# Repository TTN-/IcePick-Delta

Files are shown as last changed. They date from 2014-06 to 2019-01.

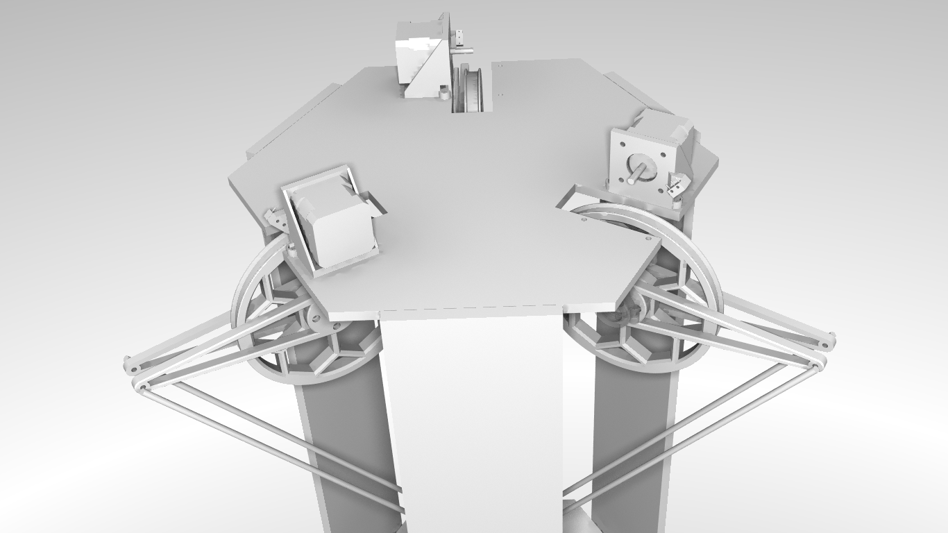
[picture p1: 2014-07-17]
Icepick Delta/Beta/Jotham/renders/assembly4.png

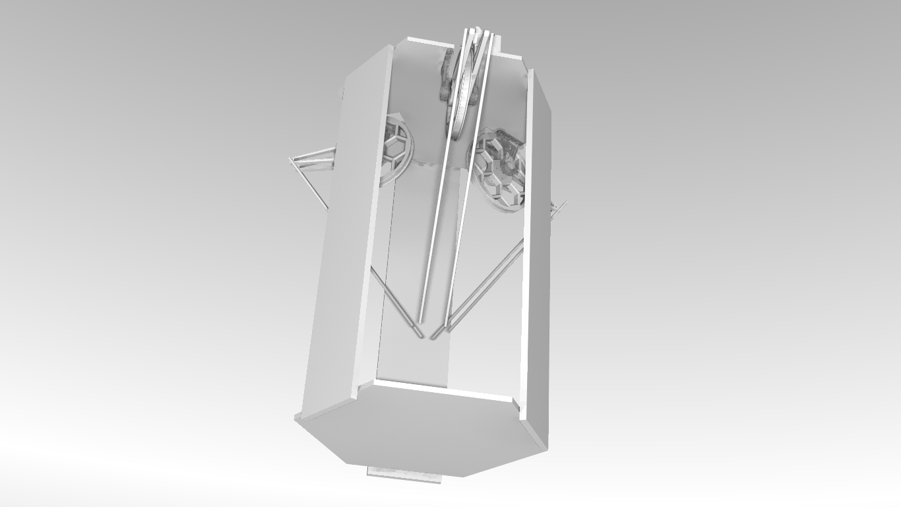
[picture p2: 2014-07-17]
Icepick Delta/Beta/Jotham/renders/assembly3.png

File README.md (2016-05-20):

IcePick Delta CAD files
=======================
I should state that this printer is NOT ready for general consumption and is HIGHLY experimental. 

Most of these parts are still being tested and revised, they may be improved without prior notice ;)

More details at the <a href="http://hackaday.io/project/1565">Icepick-delta HackaDay page.</a>

Firmware
========
Firmware for the Icepick-Delta can be found <a href="https://github.com/Laura3/Marlin/tree/Marlin_v1"> here.</a>

Contributors/Credits
============
Lots of thanks goes to the Firepick Delta team, (<a href=http://hackaday.io/project/963> project page</a> ) for being the original inspiration to this project. Thank you Lerche, Neil Jansen, Karl, Lew and Dayton Pidhirney. Without you guys this project wouldn't have existed.

Credit goes to Matt Kimbal for pulley_mounts.stl
Pulley_mount.stl and pulley_mount.FCStd are copyright of Matt Kimbal, released under gpl version 3.

Credit goes to Johann Rochell for effector.stl and effector_retractable.stl from his <a href="https://github.com/jcrocholl/kossel">Github Kossel repository.</a> are copyright of Johann Rochell, released under gpl version 3.

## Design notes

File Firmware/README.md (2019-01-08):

Marlin Firmware for Non-linear Delta 3D Printers
==================================================
This firmware is a fork of the main repository with modifications for non-linear delta printers such as the
<a href="http://hackaday.io/project/1565">Icepick Delta</a>. 

==========================
Marlin 3D Printer Firmware
==========================
Marlin has a GPL license because I believe in open development.
Please do not use this code in products (3D printers, CNC etc) that are closed source or are crippled by a patent.



Quick Information
===================
This RepRap firmware is a mashup between <a href="https://github.com/kliment/Sprinter">Sprinter</a>, <a href="https://github.com/simen/grbl/tree">grbl</a> and many original parts.

Derived from Sprinter and Grbl by Erik van der Zalm.
Sprinters lead developers are Kliment and caru.
Grbls lead developer is Simen Svale Skogsrud. Sonney Jeon (Chamnit) improved some parts of grbl
A fork by bkubicek for the Ultimaker was merged, and further development was aided by him.
Some features have been added by:
Lampmaker, Bradley Feldman, and others...

Features:

*   Interrupt based movement with real linear acceleration
*   High steprate
*   Look ahead (Keep the speed high when possible. High cornering speed)
*   Interrupt based temperature protection
*   preliminary support for Matthew Roberts advance algorithm
    For more info see: http://reprap.org/pipermail/reprap-dev/2011-May/003323.html
*   Full endstop support
*   SD Card support
*   SD Card folders (works in pronterface)
*   SD Card autostart support
*   LCD support (ideally 20x4)
*   LCD menu system for autonomous SD card printing, controlled by an click-encoder.
*   EEPROM storage of e.g. max-velocity, max-acceleration, and similar variables
*   many small but handy things originating from bkubicek's fork.
*   Arc support
*   Temperature oversampling
*   Dynamic Temperature setpointing aka "AutoTemp"
*   Support for QTMarlin, a very beta GUI for PID-tuning and velocity-acceleration testing. https://github.com/bkubicek/QTMarlin
*   Endstop trigger reporting to the host software.
*   Updated sdcardlib
*   Heater power reporting. Useful for PID monitoring.
*   PID tuning
*   CoreXY kinematics (www.corexy.com/theory.html)
*   Delta kinematics
*   Dual X-carriage support for multiple extruder systems
*   Configurable serial port to support connection of wireless adaptors.
*   Automatic operation of extruder/cold-end cooling fans based on nozzle temperature
*   RC Servo Support, specify angle or duration for continuous rotation servos.
*   Bed Auto Leveling.

The default baudrate is 250000. This baudrate has less jitter and hence errors than the usual 115200 baud, but is less supported by drivers and host-environments.

Differences and additions to the already good Sprinter firmware:
================================================================

*Look-ahead:*

Marlin has look-ahead. While sprinter has to break and re-accelerate at each corner,
lookahead will only decelerate and accelerate to a velocity,
so that the change in vectorial velocity magnitude is less than the xy_jerk_velocity.
This is only possible, if some future moves are already processed, hence the name.
It leads to less over-deposition at corners, especially at flat angles.

*Arc support:*

Slic3r can find curves that, although broken into segments, were ment to describe an arc.
Marlin is able to print those arcs. The advantage is the firmware can choose the resolution,
and can perform the arc with nearly constant velocity, resulting in a nice finish.
Also, less serial communication is needed.

*Temperature Oversampling:*

To reduce noise and make the PID-differential term more useful, 16 ADC conversion results are averaged.

*AutoTemp:*

If your gcode contains a wide spread of extruder velocities, or you realtime change the building speed, the temperature should be changed accordingly.
Usually, higher speed requires higher temperature.
This can now be performed by the AutoTemp function
By calling M109 S<mintemp> T<maxtemp> F<factor> you enter the autotemp mode.

You can leave it by calling M109 without any F.
If active, the maximal extruder stepper rate of all buffered moves will be calculated, and named "maxerate" [steps/sec].
The wanted temperature then will be set to t=tempmin+factor*maxerate, while being limited between tempmin and tempmax.
If the target temperature is set manually or by gcode to a value less then tempmin, it will be kept without change.
Ideally, your gcode can be completely free of temperature controls, apart from a M109 S T F in the start.gcode, and a M109 S0 in the end.gcode.

*EEPROM:*

If you know your PID values, the acceleration and max-velocities of your unique machine, you can set them, and finally store them in the EEPROM.
After each reboot, it will magically load them from EEPROM, independent what your Configuration.h says.

*LCD Menu:*

If your hardware supports it, you can build yourself a LCD-CardReader+Click+encoder combination. It will enable you to realtime tune temperatures,
accelerations, velocities, flow rates, select and print files from the SD card, preheat, disable the steppers, and do other fancy stuff.
One working hardware is documented here: http://www.thingiverse.com/thing:12663
Also, with just a 20x4 or 16x2 display, useful data is shown.

*SD card folders:*

If you have an SD card reader attached to your controller, also folders work now. Listing the files in pronterface will show "/path/subpath/file.g".
You can write to file in a subfolder by specifying a similar text using small letters in the path.
Also, backup copies of various operating systems are hidden, as well as files not ending with ".g".

*SD card folders:*

If you place a file auto[0-9].g into the root of the sd card, it will be automatically executed if you boot the printer. The same file will be executed by selecting "Autostart" from the menu.
First *0 will be performed, than *1 and so on. That way, you can heat up or even print automatically without user interaction.

*Endstop trigger reporting:*

If an endstop is hit while moving towards the endstop, the location at which the firmware thinks that the endstop was triggered is outputed on the serial port.
This is useful, because the user gets a warning message.
However, also tools like QTMarlin can use this for finding acceptable combinations of velocity+acceleration.

*Coding paradigm:*

Not relevant from a user side, but Marlin was split into thematic junks, and has tried to partially enforced private variables.
This is intended to make it clearer, what interacts which what, and leads to a higher level of modularization.
We think that this is a useful prestep for porting this firmware to e.g. an ARM platform in the future.
A lot of RAM (with enabled LCD ~2200 bytes) was saved by storing char []="some message" in Program memory.
In the serial communication, a #define based level of abstraction was enforced, so that it is clear that
some transfer is information (usually beginning with "echo:"), an error "error:", or just normal protocol,
necessary for backwards compatibility.

*Interrupt based temperature measurements:*

An interrupt is used to manage ADC conversions, and enforce checking for critical temperatures.
This leads to less blocking in the heater management routine.

Implemented G Codes:
====================

*  G0  -> G1
*  G1  - Coordinated Movement X Y Z E
*  G2  - CW ARC
*  G3  - CCW ARC
*  G4  - Dwell S<seconds> or P<milliseconds>
*  G10 - retract filament according to settings of M207
*  G11 - retract recover filament according to settings of M208
*  G28 - Home all Axis
*  G29 - Detailed Z-Probe, probes the bed at 3 points.  You must de at the home position for this to work correctly.
*  G30 - Single Z Probe, probes bed at current XY location.
*  G90 - Use Absolute Coordinates
*  G91 - Use Relative Coordinates
*  G92 - Set current position to cordinates given

M Codes
*  M0   - Unconditional stop - Wait for user to press a button on the LCD (Only if ULTRA_LCD is enabled)
*  M1   - Same as M0
*  M17  - Enable/Power all stepper motors
*  M18  - Disable all stepper motors; same as M84
*  M20  - List SD card
*  M21  - Init SD card
*  M22  - Release SD card
*  M23  - Select SD file (M23 filename.g)
*  M24  - Start/resume SD print
*  M25  - Pause SD print
*  M26  - Set SD position in bytes (M26 S12345)
*  M27  - Report SD print status
*  M28  - Start SD write (M28 filename.g)
*  M29  - Stop SD write
*  M30  - Delete file from SD (M30 filename.g)
*  M31  - Output time since last M109 or SD card start to serial
*  M32  - Select file and start SD print (Can be used when printing from SD card)
*  M42  - Change pin status via gcode Use M42 Px Sy to set pin x to value y, when omitting Px the onboard led will be used.
*  M80  - Turn on Power Supply
*  M81  - Turn off Power Supply
*  M82  - Set E codes absolute (default)
*  M83  - Set E codes relative while in Absolute Coordinates (G90) mode
*  M84  - Disable steppers until next move, or use S<seconds> to specify an inactivity timeout, after which the steppers will be disabled.  S0 to disable the timeout.
*  M85  - Set inactivity shutdown timer with parameter S<seconds>. To disable set zero (default)
*  M92  - Set axis_steps_per_unit - same syntax as G92
*  M104 - Set extruder target temp
*  M105 - Read current temp
*  M106 - Fan on
*  M107 - Fan off
*  M109 - Sxxx Wait for extruder current temp to reach target temp. Waits only when heating
*         Rxxx Wait for extruder current temp to reach target temp. Waits when heating and cooling
*  M114 - Output current position to serial port
*  M115 - Capabilities string
*  M117 - display message
*  M119 - Output Endstop status to serial port
*  M126 - Solenoid Air Valve Open (BariCUDA support by jmil)
*  M127 - Solenoid Air Valve Closed (BariCUDA vent to atmospheric pressure by jmil)
*  M128 - EtoP Open (BariCUDA EtoP = electricity to air pressure transducer by jmil)
*  M129 - EtoP Closed (BariCUDA EtoP = electricity to air pressure transducer by jmil)
*  M140 - Set bed target temp
*  M190 - Sxxx Wait for bed current temp to reach target temp. Waits only when heating
*         Rxxx Wait for bed current temp to reach target temp. Waits when heating and cooling
*  M200 - Set filament diameter
*  M201 - Set max acceleration in units/s^2 for print moves (M201 X1000 Y1000)
*  M202 - Set max acceleration in units/s^2 for travel moves (M202 X1000 Y1000) Unused in Marlin!!
*  M203 - Set maximum feedrate that your machine can sustain (M203 X200 Y200 Z300 E10000) in mm/sec
*  M204 - Set default acceleration: S normal moves T filament only moves (M204 S3000 T7000) im mm/sec^2  also sets minimum segment time in ms (B20000) to prevent buffer underruns and M20 minimum feedrate
*  M205 -  advanced settings:  minimum travel speed S=while printing T=travel only,  B=minimum segment time X= maximum xy jerk, Z=maximum Z jerk, E=maximum E jerk
*  M206 - set additional homeing offset
*  M207 - set retract length S[positive mm] F[feedrate mm/sec] Z[additional zlift/hop]
*  M208 - set recover=unretract length S[positive mm surplus to the M207 S*] F[feedrate mm/sec]
*  M209 - S<1=true/0=false> enable automatic retract detect if the slicer did not support G10/11: every normal extrude-only move will be classified as retract depending on the direction.
*  M218 - set hotend offset (in mm): T<extruder_number> X<offset_on_X> Y<offset_on_Y>
*  M220 S<factor in percent>- set speed factor override percentage
*  M221 S<factor in percent>- set extrude factor override percentage
*  M240 - Trigger a camera to take a photograph
*  M280 - Position an RC Servo P<index> S<angle/microseconds>, ommit S to report back current angle
*  M300 - Play beepsound S<frequency Hz> P<duration ms>
*  M301 - Set PID parameters P I and D
*  M302 - Allow cold extrudes
*  M303 - PID relay autotune S<temperature> sets the target temperature. (default target temperature = 150C)
*  M304 - Set bed PID parameters P I and D
*  M400 - Finish all moves
*  M401 - Lower z-probe if present
*  M402 - Raise z-probe if present
*  M500 - stores paramters in EEPROM
*  M501 - reads parameters from EEPROM (if you need reset them after you changed them temporarily).
*  M502 - reverts to the default "factory settings".  You still need to store them in EEPROM afterwards if you want to.
*  M503 - print the current settings (from memory not from eeprom)
*  M540 - Use S[0|1] to enable or disable the stop SD card print on endstop hit (requires ABORT_ON_ENDSTOP_HIT_FEATURE_ENABLED)
*  M600 - Pause for filament change X[pos] Y[pos] Z[relative lift] E[initial retract] L[later retract distance for removal]
*  M907 - Set digital trimpot motor current using axis codes.
*  M908 - Control digital trimpot directly.
*  M350 - Set microstepping mode.
*  M351 - Toggle MS1 MS2 pins directly.
*  M928 - Start SD logging (M928 filename.g) - ended by M29
*  M999 - Restart after being stopped by error

Configuring and compilation:
============================

Install the arduino software IDE/toolset v23 (Some configurations also work with 1.x.x)
   http://www.arduino.cc/en/Main/Software

Download the Marlin firmware
   https://github.com/ErikZalm/Marlin/tree/Marlin_v1
   Use the "Download Zip" button on the right.

For gen6/gen7 and sanguinololu the Sanguino directory in the Marlin dir needs to be copied to the arduino environment.
  copy ArduinoAddons\Arduino_x.x.x\sanguino <arduino home>\hardware\Sanguino

Start the arduino IDE.
Select Tools -> Board -> Arduino Mega 2560    or your microcontroller
Select the correct serial port in Tools ->Serial Port
Open Marlin.pde

Click the Verify/Compile button

Click the Upload button
If all goes well the firmware is uploading

That's ok.  Enjoy Silky Smooth Printing.

===============================================
Instructions for configuring Bed Auto Leveling
===============================================
Uncomment the "ENABLE_AUTO_BED_LEVELING" define (commented by default)

You will probably need a swivel Z-MIN endstop in the extruder. A rc servo do a great job.
Check the system working here: http://www.youtube.com/watch?v=3IKMeOYz-1Q (Enable English subtitles)
Teasing ;-) video: http://www.youtube.com/watch?v=x8eqSQNAyro

In order to get the servo working, you need to enable:

* \#define NUM_SERVOS 1 // Servo index starts with 0 for M280 command

* \#define SERVO_ENDSTOPS {-1, -1, 0} // Servo index for X, Y, Z. Disable with -1

* \#define SERVO_ENDSTOP_ANGLES {0,0, 0,0, 165,60} // X,Y,Z Axis Extend and Retract angles

The first define tells firmware how many servos you have.
The second tells what axis this servo will be attached to. In the example above, we have a servo in Z axis.
The third one tells the angle in 2 situations: Probing (165º) and resting (60º). Check this with command M280 P0 S{angle} (example: M280 P0 S60 moves the servo to 60º)

*For RAMPS users:*
By default, RAMPS have no power on servo bus (if you happen to have a multimeter, check the voltage on servo power pins).
In order to get the servo working, you need to supply 5V to 5V pin.. You can do it using your power supply (if it has a 5V output) or jumping the "Vcc" from Arduino to the 5V RAMPS rail.
These 2 pins are located just between the Reset Button and the yellow fuses... There are marks in the board showing 5V and VCC.. just connect them..
If jumping the arduino Vcc do RAMPS 5V rail, take care to not use a power hungry servo, otherwise you will cause a blackout in the arduino board ;-)

Next you need to define the Z endstop (probe) offset from hotend.
My preferred method:

* a) Make a small mark in the bed with a marker/felt-tip pen.
* b) Place the hotend tip as *exactly* as possible on the mark, touching the bed. Raise the hotend 0.1mm (a regular paper thickness) and zero all axis (G92 X0 Y0 Z0);
* d) Raise the hotend 10mm (or more) for probe clearance, lower the Z probe (Z-Endstop) with M401 and place it just on that mark by moving X, Y and Z;
* e) Lower the Z in 0.1mm steps, with the probe always touching the mark (it may be necessary to adjust X and Y as well) until you hear the "click" meaning the mechanical endstop was trigged. You can confirm with M119;
* f) Now you have the probe in the same place as your hotend tip was before. Perform a M114 and write down the values, for example: X:24.3 Y:-31.4 Z:5.1;
* g) You can raise the z probe with M402 command;
* h) Fill the defines bellow multiplying the values by "-1" (just change the signal)

* \#define X_PROBE_OFFSET_FROM_EXTRUDER -24.3
* \#define Y_PROBE_OFFSET_FROM_EXTRUDER 31.4
* \#define Z_PROBE_OFFSET_FROM_EXTRUDER -5.1

The following options define the probing positions. These are good starting values.
I recommend to keep a better clearance from borders in the first run and then make the probes as close as possible to borders:

* \#define LEFT_PROBE_BED_POSITION 30
* \#define RIGHT_PROBE_BED_POSITION 140
* \#define BACK_PROBE_BED_POSITION 140
* \#define FRONT_PROBE_BED_POSITION 30

A few more options:

* \#define XY_TRAVEL_SPEED 6000

X and Y axis travel speed between probes, in mm/min.
Bear in mind that really fast moves may render step skipping. 6000 mm/min (100mm/s) is a good value.

* \#define Z_RAISE_BEFORE_PROBING 10
* \#define Z_RAISE_BETWEEN_PROBINGS 10

The Z axis is lifted when traveling to the first probe point by Z_RAISE_BEFORE_PROBING value
and then lifted when traveling from first to second and second to third point by Z_RAISE_BETWEEN_PROBINGS.
All values are in mm as usual. 

That's it.. enjoy never having to calibrate your Z endstop neither leveling your bed by hand anymore ;-)

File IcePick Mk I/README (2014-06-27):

TODO:

CAD:

lower bearing brackets DONE

upper motor mount for motors DONE

spacers in between motor mounts

large pulley

upper arms, the 'fingers' (150mm long)

end effector (something like the kossel mini effector with the bed leveling probe)

endstop switch mounts

SOFTWARE:
make a post processing script for all gcodes, could be done in python, or a cura plugin

OR

make a function in Marlin which will take on inverse kinematic deltas (this is actually the proper way to do it, post proccessing script will do fine for now..)

bed leveling (not going to work, unless we teach marlin inverse kinematics)

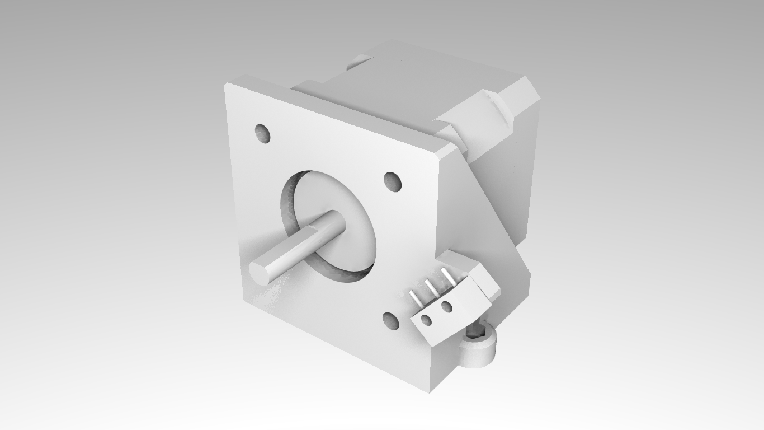
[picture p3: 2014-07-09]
Icepick Delta/Beta/Jotham/renders/motor_mount_render.png

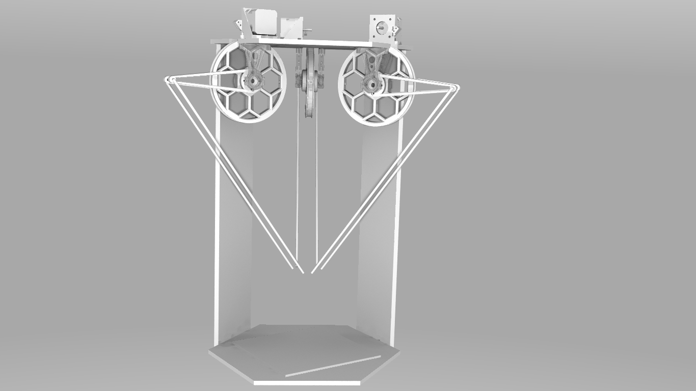
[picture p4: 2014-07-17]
Icepick Delta/Beta/Jotham/renders/render6.png

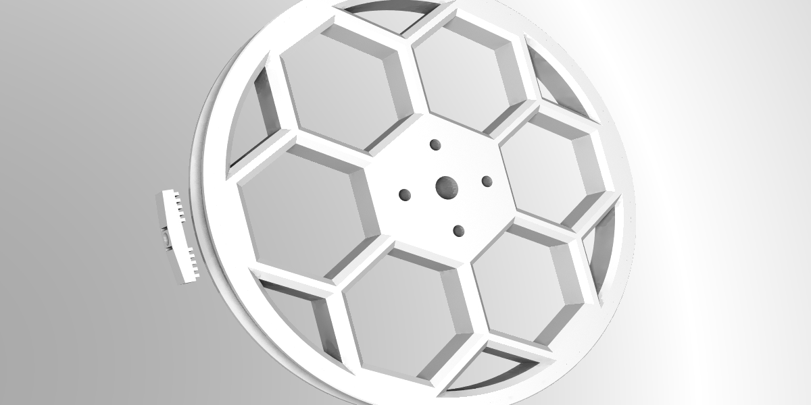
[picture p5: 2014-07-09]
Icepick Delta/Beta/Jotham/renders/pulley - v0.9 render.png

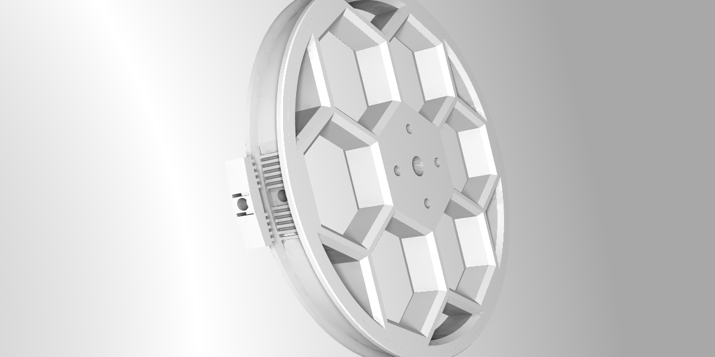
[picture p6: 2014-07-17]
Icepick Delta/Beta/Jotham/renders/pulley.png

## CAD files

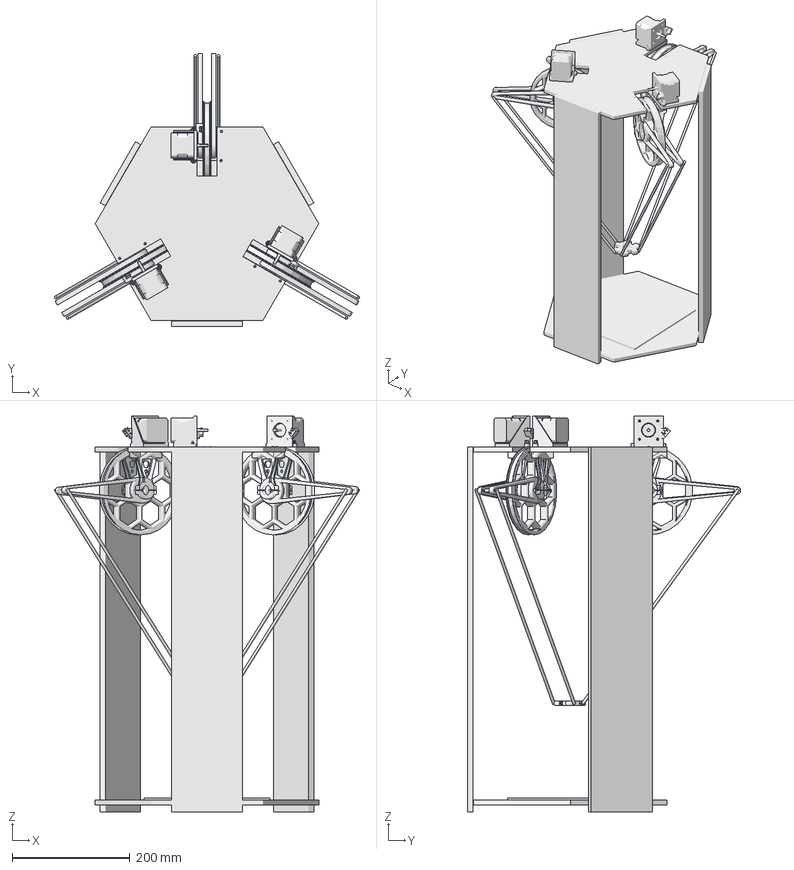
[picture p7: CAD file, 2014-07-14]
assembly.FCStd
518.8 x 464.5 x 673.0 mm
motor_mount001
motor_mount002
motor_mount003
axlemount_L002
axlemount_R002
pulley
pulley001
pulley002
axlemount_R1
arm_004
arm_005
arm_006
upper_arm_R1
upper_arm_R2
upper_arm_R004
upper_arm_R005
upper_arm_R006
axlemount_R003
frame
axlemount_R004
axlemount_R005
axlemount_R006
upper_arm_R007
upper_arm_R008
upper_arm_R009
effector

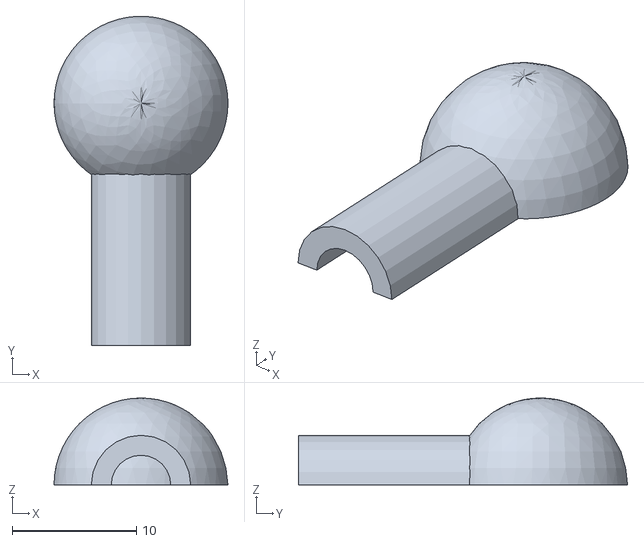
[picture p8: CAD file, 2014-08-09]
universal joint concept 2/socket2.2.stl
14.0 x 26.5 x 7.00

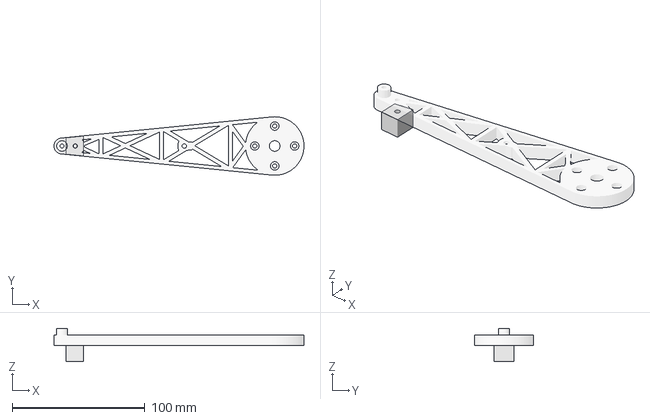
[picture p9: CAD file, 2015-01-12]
upperarm_spacer.FCStd
188.0 x 44.0 x 25.0 mm
upperarm_160mm

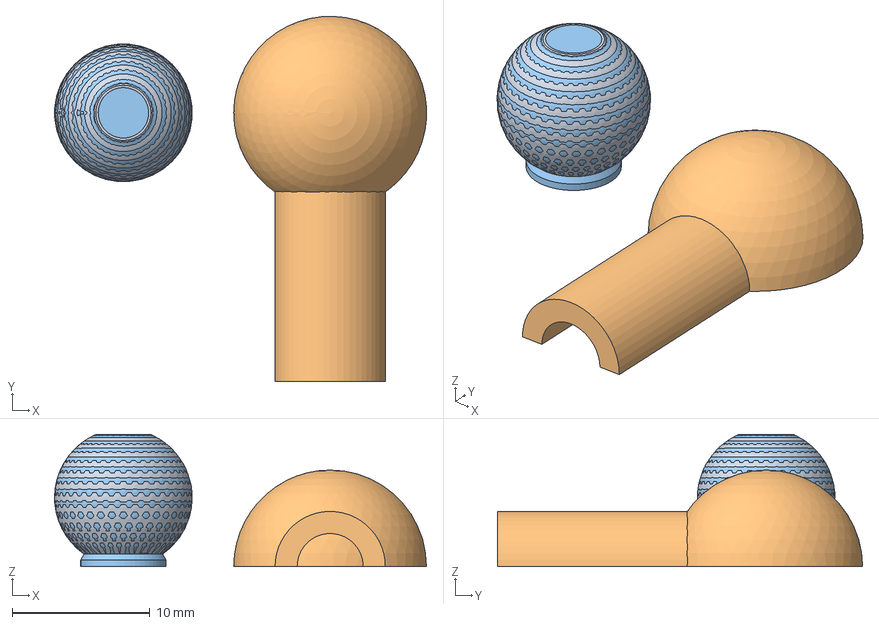
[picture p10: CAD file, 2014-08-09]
universal joint concept 2/joint concept2.2.FCStd
27.0 x 26.5 x 9.58 mm
ball joint

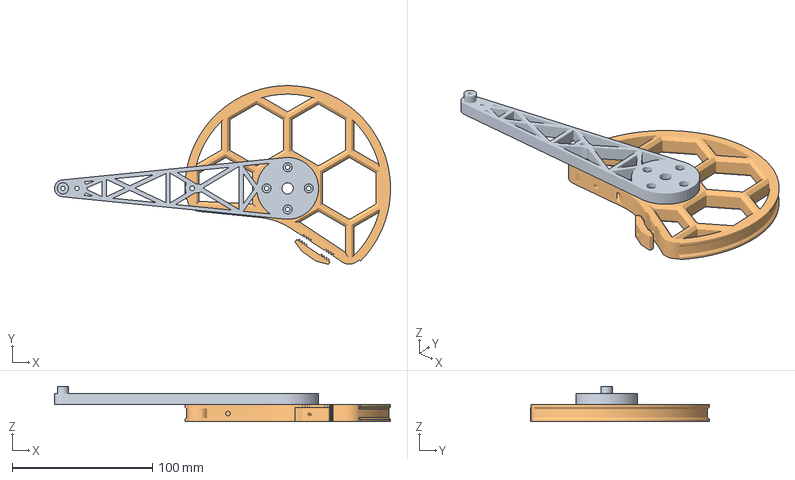
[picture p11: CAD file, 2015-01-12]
upperarm_160mm.FCStd
239.2 x 127.2 x 25.0 mm
pulley_half_v0.9.4

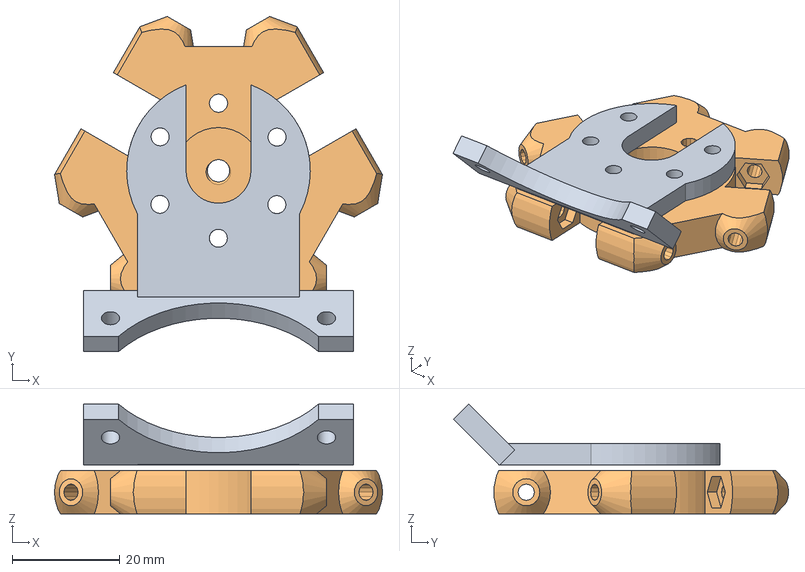
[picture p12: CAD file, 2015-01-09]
effector_jhead_clamp+fan_mount.FCStd
60.7 x 62.1 x 20.3 mm
effector

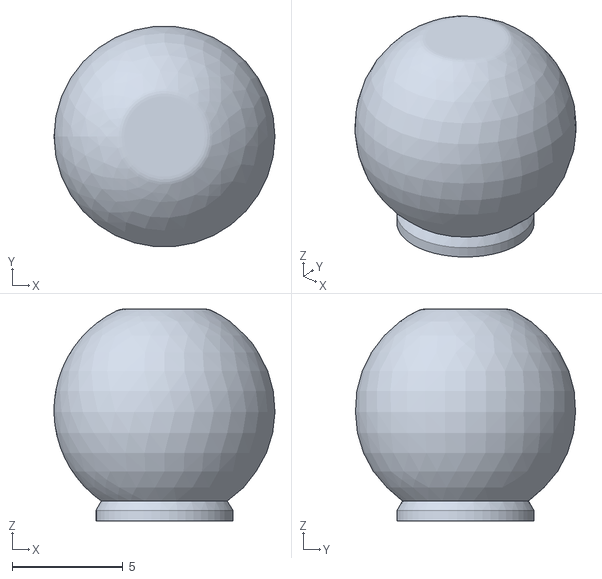
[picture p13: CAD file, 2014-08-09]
universal joint concept 2/balljoint2.2.stl
10.00 x 9.96 x 9.58

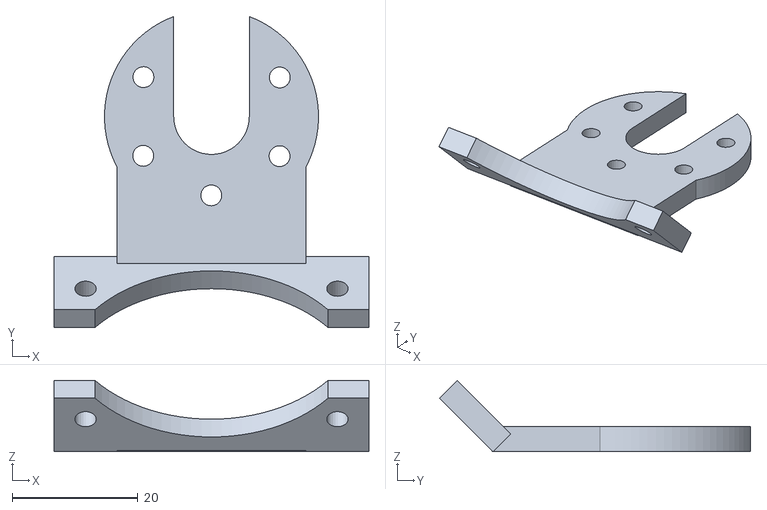
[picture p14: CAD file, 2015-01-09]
effctor_clamp+fan_mount.stl
50.0 x 49.4 x 11.3

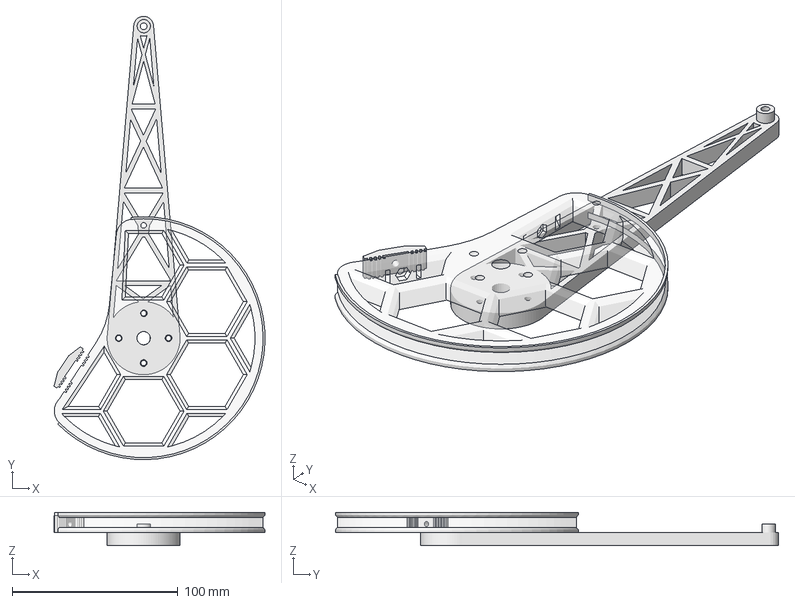
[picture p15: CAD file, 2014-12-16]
pulley_half_v0.9.4.FCStd
127.2 x 267.1 x 20.0 mm
belt_clamp
pulley_ridges001
upperarm v2.2.2

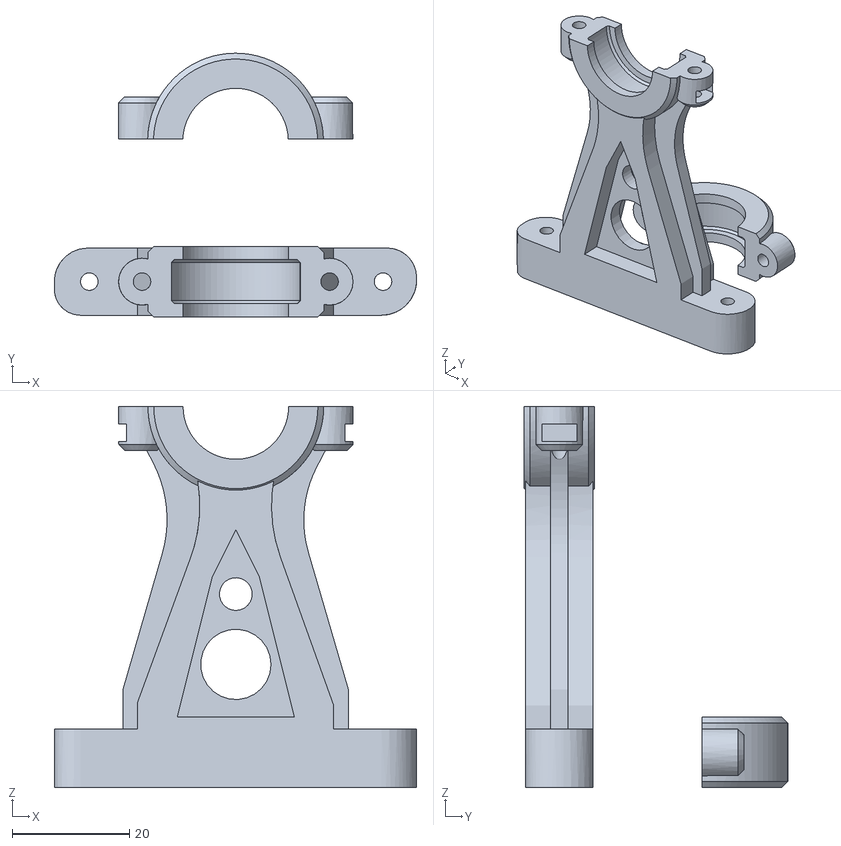
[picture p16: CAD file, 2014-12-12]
pulley_mount.stl
61.8 x 45.0 x 65.0

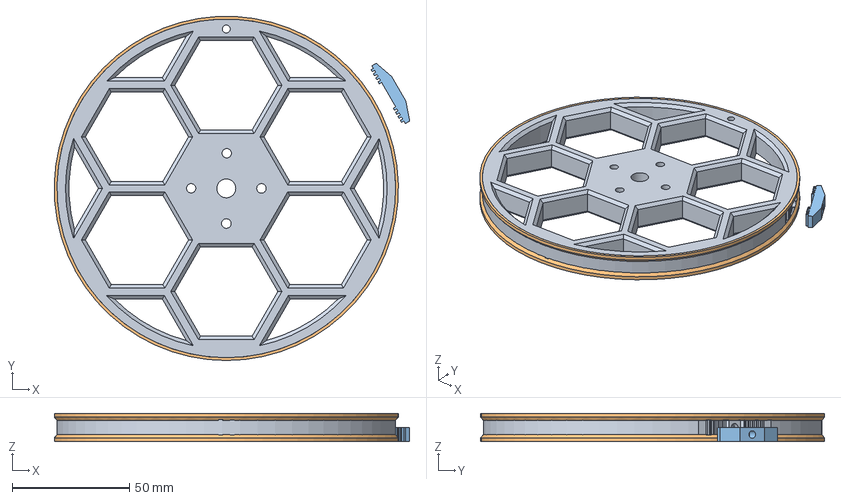
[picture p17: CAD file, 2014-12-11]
pulley_v0.9.4.FCStd
151.7 x 146.8 x 12.0 mm
pulley001
ridges
belt_clamp

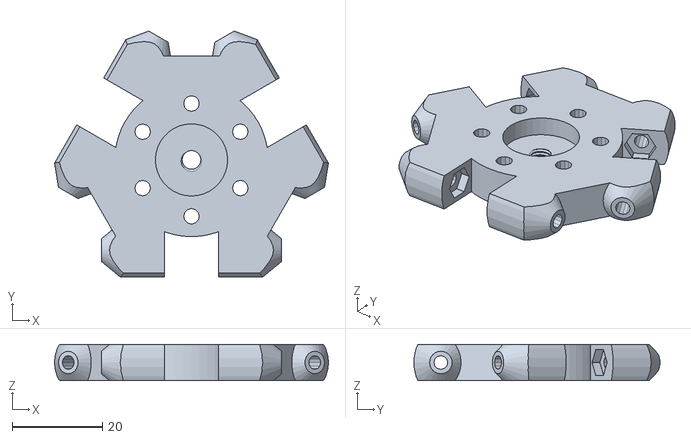
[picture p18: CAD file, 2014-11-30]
effector.stl
60.7 x 54.5 x 8.00

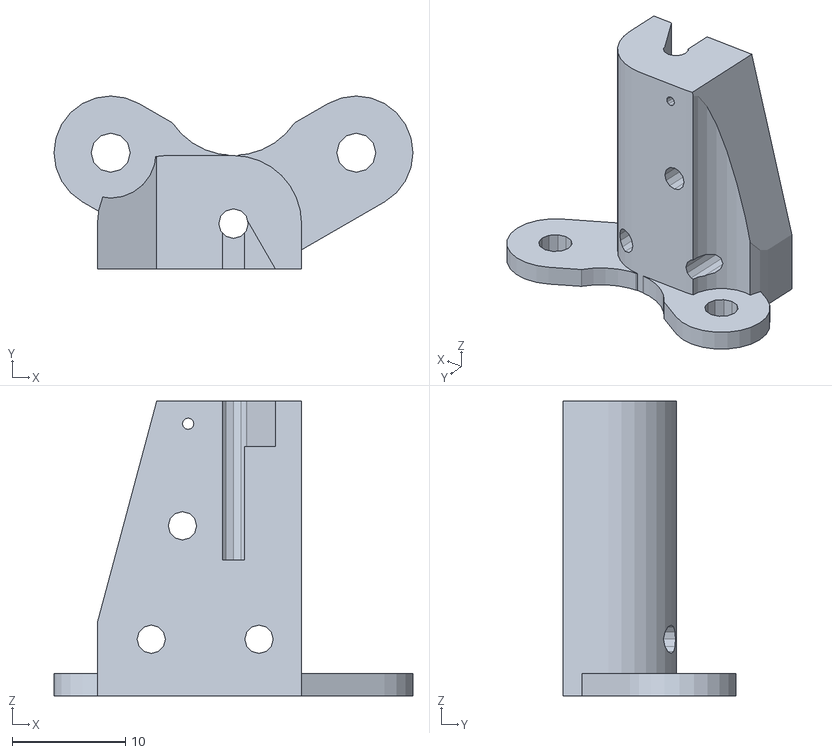
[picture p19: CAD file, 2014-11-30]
effector_retractable.stl
31.7 x 15.2 x 26.0

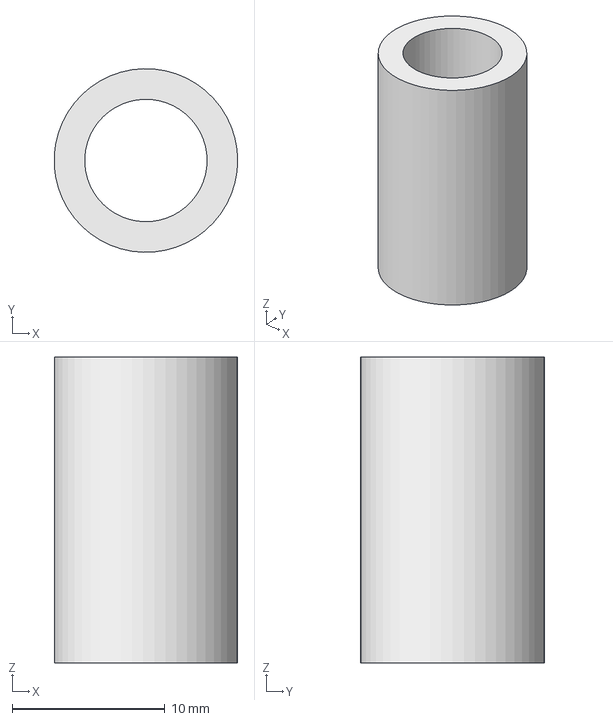
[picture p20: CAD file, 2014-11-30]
effector_diagonal_rod_tube.FCStd
12.0 x 12.0 x 20.0 mm

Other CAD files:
effector_diagonal_rod_tubes.stl
motor_mount.FCStd
effector_jhead_clamp.FCStd
jhead_clamp.FCStd
endstop_screw_mount.FCStd
endstop_screw_mount.stl
frame_mockup (outdated).FCStd
frame_mockup.FCStd
motor_mount.stl
pulley_half_v0.9.4.stl
pulley_v0.9.4.stl
upperarm_160mm.stl
upperarm_old_180_160_130mm lengths.FCStd
upperarm_old_180_160_130mm lengths.stl
upperarm_spacer.stl

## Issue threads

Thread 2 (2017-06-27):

DELTA NOT MOVING PROPERLY

3ddev-j, 2017-06-27:
Hi TTN, you have made a really nice project in this delta inverse kinematics firmware, but i'm in doubt on some codelines of your marlin that are driving me crazy on my delta printer.

first of all, i'm not good in english its dificult to me understand some words on yours coment at marlin v1.1, so....

Could you please explain me what kind of measures i should do on this first code part, to get my printer working?

// Enable DELTA kinematics and most of the default configuration for Deltas
#define DELTA

// NOTE NB all values for DELTA_* values MUST be floating point, so always have a decimal point in them

// Make delta curves from many straight lines (linear interpolation).
// This is a trade-off between visible corners (not enough segments)
// and processor overload (too many expensive calulations).
#define DELTA_SEGMENTS_PER_SECOND 40

// Horizontal offset of the pulley axle centres from the mounting plate centre
#define BASE_RADIUS 80.600
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

 // you mean the center of machine to each pulley (large ones) center?

// what is the meaning of mouting plate? is the heatbed?

// Horizontal radius of the end effector centre to the tangentline where the joints are
// making this value large will make prints scale larger in xy direction as z gets higher
#define END_EFFECTOR_RADIUS 20.000 // 20.0mm for kossel end effector (used in the icepick delta)

// Center-to-center distance of the holes in the diagonal push rods.
// this has to EXACT. 1mm off and the hotend will far be too high or low in the middle of the printbed relative to edges
#define DELTA_DIAGONAL_ROD 325.000 // distance of the carbon fiber rods center to center?

// upperarm length
// if your hotend is close/too far from the bed near the edges, check this is correct
#define DELTA_ARM_LENGTH 160.000// i used original icepick one

// distance from home position to bed.
// if this value doesn't adjust linearly for you, it means DELTA_DIAGONL_ROD and/or DELTA_ARM_LENGTH is wrong
#define Z_HOME_HEIGTH 265.580
// what does linearly" means?

// vertical distance from vertical midpoint of the end effector to mounting plate
// this controls whether objects get narrower or wider as it gets taller
// and if set incorrectly, will contribute to the end effector not moving across the bed linearly
// towards the edges of the print bed this will become more apparent
// will also affect how far the machine thinks it can reach
// Too large value: leaning outward
// Too small value: leaning inward
#define END_EFFECTOR_TO_MOUNTPLATE 34.0

// this should be the same as Z_HOME_HEITGH?

// vertical distance from the pulley axles to the mounting plate
#define PULLEY_MOUNT_HEIGHT 448.00

Tnks!

Have i nice day hope u understood me :)

TTN-, 2017-11-04:
Hi, sorry I never got back to you. Better late than never?
Its been 2 years since I wrote this code so I'll do my best to remember.

Base radius:
So if you draw a circle going through all of the big pulley axle holes, that is the radius we are talking about.

----|||---- <- pulley1 on axle. Base radius is distance from this axle to the center
       |
       |
     /  \
   /      \
2          3  <- pulleys 2 and 3

> // you mean the center of machine to each pulley (large ones) center?
Yes.

>// what is the meaning of mouting plate? is the heatbed?
For me all the pulleys are mounted to a wooden plate. This variable is the distance from that plate to my pulley axle centers. You can just set it to 0.0 for your case.

>#define DELTA_DIAGONAL_ROD 325.000 // distance of the carbon fiber rods center to center?
Yes.

>// what does linearly" means?
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
I think its best explained like this ^

>#define END_EFFECTOR_TO_MOUNTPLATE 34.0
>// this should be the same as Z_HOME_HEITGH?
This is the distance from your effector rod screw holes to your mounting plate. You can just use the distance from your effector rod screw holes to the center of your axles.

This machine is a pain in the !@#$ to calibrate. Its very time consuming but I managed to get in 0.2mm spec. It takes a lot of work. All the variables have comments explaining what changing it does but if you have more questions do ask and I will make an effort to reply in a timely manner.

TTN-, 2019-03-09:
Explained as required :-) if you have any more questions, please reopen this issue or file a new one, thanks!

Closed 2019-03-09.

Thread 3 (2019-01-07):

Missing firmware

asharkinwater, 2019-01-07:
Hey TTN,
Great project! I really like your design and am considering making a similar style delta. I was wondering if you could upload the firmware for this project or point me in the direction of where I can find it. It seems that the [page]( https://github.com/Laura3/Marlin/tree/Marlin_v1) you provided no longer exists.

Thank you for your time,
August

TTN-, 2019-01-07:
No worries mate. I'll upload it tonight :-)

TTN-, 2019-01-08:
@asharkinwater thanks for letting me know the link got broken. I've added it to the repo here in the firmware folder. From memory it should just work, though its been a few years: https://github.com/TTN-/IcePick-Delta/tree/master/Firmware

I do have to warn you calibrating these things is a pain in the butt, I got it narrowed down to 0.2mm accuracy but only after I machined the pulleys round on a lathe (my badly built printer at the time didn't produce round circles).. You need very good precision to get it right. Good fun though :-) Let me know how you go!

asharkinwater, 2019-01-08:
Will do! I Just tested the firmware on a ramps board and some steppers I had laying around and everything seems to be working just fine.  I look forward to building one over the next month or so.  Cheers!

TTN-, 2019-03-09:
Files uploaded as requested, issue resolved :)

Closed 2019-03-09.

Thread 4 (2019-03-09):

endstopbrackets?

Konole, 2019-03-09:
Could you share the mounting brackets for the endstops? I can't find them in the files.
Thanks!

TTN-, 2019-03-12:
I can't seem to find them in the folder on my PC. Sorry about that!

Are you able to model them up yourself?

Otherwise, if you make a paper drawing with your required dimensions and send it to me, I can model it for you and upload it for you to use. Can't guarantee it'll be done anytime soon though.

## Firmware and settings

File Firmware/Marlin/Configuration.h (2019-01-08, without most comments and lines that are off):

#define CONFIGURATION_H
#define STRING_VERSION_CONFIG_H __DATE__ " " __TIME__ // build date and time
#define STRING_CONFIG_H_AUTHOR "(none, Icepick Delta Config)" // Who made the changes.
#define SERIAL_PORT 0
#define BAUDRATE 115200
#define MOTHERBOARD 33
#define EXTRUDERS 1
#define POWER_SUPPLY 1
#define DELTA
#define DELTA_SEGMENTS_PER_SECOND 40
#define BASE_RADIUS 135.0
#define END_EFFECTOR_RADIUS 20.0 // 20.0mm for kossel end effector (used in the icepick delta)
#define DELTA_DIAGONAL_ROD 302.0
#define DELTA_ARM_LENGTH 160.0
#define Z_HOME_HEIGTH 245.0
#define END_EFFECTOR_TO_MOUNTPLATE 190.0
#define PULLEY_MOUNT_HEIGHT 63.5
#define DELTA_SQRT3 1.732050807
#define DELTA_PI 3.141592653 // PI
#define DELTA_SIN120 DELTA_SQRT3/2.0
#define DELTA_COS120 -0.5
#define DELTA_TAN60 DELTA_SQRT3
#define DELTA_SIN30 0.5
#define DELTA_TAN30 1/DELTA_SQRT3
#define BASE_SIDE BASE_RADIUS*2*sqrt(3)
#define END_EFFECTOR_SIDE END_EFFECTOR_RADIUS*2*sqrt(3)
#define DELTA_HOME_POS MANUAL_Z_HOME_POS - (END_EFFECTOR_TO_MOUNTPLATE - PULLEY_MOUNT_HEIGHT)
#define DELTA_RADIUS 20
#define TEMP_SENSOR_0 1
#define TEMP_SENSOR_1 0
#define TEMP_SENSOR_2 0
#define TEMP_SENSOR_BED 1
#define MAX_REDUNDANT_TEMP_SENSOR_DIFF 10
#define TEMP_RESIDENCY_TIME 10  // (seconds)
#define TEMP_HYSTERESIS 3       // (degC) range of +/- temperatures considered "close" to the target one
#define TEMP_WINDOW     1       // (degC) Window around target to start the residency timer x degC early.
#define HEATER_0_MINTEMP 5
#define HEATER_1_MINTEMP 5
#define HEATER_2_MINTEMP 5
#define BED_MINTEMP 5
#define HEATER_0_MAXTEMP 245
#define HEATER_1_MAXTEMP 245
#define HEATER_2_MAXTEMP 245
#define BED_MAXTEMP 150
#define PIDTEMP
#define BANG_MAX 170 // limits current to nozzle while in bang-bang mode; 255=full current
#define PID_MAX 170 // limits current to nozzle while PID is active (see PID_FUNCTIONAL_RANGE below); 255=full current
  #define PID_FUNCTIONAL_RANGE 10 // If the temperature difference between the target temperature and the actual temperature
  #define PID_INTEGRAL_DRIVE_MAX 255  //limit for the integral term
  #define K1 0.95 //smoothing factor within the PID
  #define PID_dT ((OVERSAMPLENR * 10.0)/(F_CPU / 64.0 / 256.0)) //sampling period of the temperature routine
    #define  DEFAULT_Kp 12.47
    #define  DEFAULT_Ki 1.44
    #define  DEFAULT_Kd 27.08
#define MAX_BED_POWER 255 // limits duty cycle to bed; 255=full current
#define PREVENT_DANGEROUS_EXTRUDE
#define PREVENT_LENGTHY_EXTRUDE
#define EXTRUDE_MINTEMP 150
#define EXTRUDE_MAXLENGTH (X_MAX_LENGTH+Y_MAX_LENGTH) //prevent extrusion of very large distances.
#define ENDSTOPPULLUPS // Comment this out (using // at the start of the line) to disable the endstop pullup resistors
  #define ENDSTOPPULLUP_XMAX
  #define ENDSTOPPULLUP_YMAX
  #define ENDSTOPPULLUP_ZMAX
  #define ENDSTOPPULLUP_ZMIN
const bool X_MIN_ENDSTOP_INVERTING = false; // set to true to invert the logic of the endstop.
const bool Y_MIN_ENDSTOP_INVERTING = false; // set to true to invert the logic of the endstop.
const bool Z_MIN_ENDSTOP_INVERTING = false; // set to true to invert the logic of the endstop.
const bool X_MAX_ENDSTOP_INVERTING = false; // set to true to invert the logic of the endstop.
const bool Y_MAX_ENDSTOP_INVERTING = false; // set to true to invert the logic of the endstop.
const bool Z_MAX_ENDSTOP_INVERTING = false; // set to true to invert the logic of the endstop.
#if defined(COREXY) && !defined(DISABLE_MAX_ENDSTOPS)
  #define DISABLE_MAX_ENDSTOPS
#endif
#define X_ENABLE_ON 0
#define Y_ENABLE_ON 0
#define Z_ENABLE_ON 0
#define E_ENABLE_ON 0 // For all extruders
#define DISABLE_X false
#define DISABLE_Y false
#define DISABLE_Z false
#define DISABLE_E false // For all extruders
#define DISABLE_INACTIVE_EXTRUDER true //disable only inactive extruders and keep active extruder enabled
#define INVERT_X_DIR false // DELTA does not invert
#define INVERT_Y_DIR false
#define INVERT_Z_DIR false
#define INVERT_E0_DIR true   // for direct drive extruder v9 set to true, for geared extruder set to false
#define INVERT_E1_DIR false    // for direct drive extruder v9 set to true, for geared extruder set to false
#define INVERT_E2_DIR false   // for direct drive extruder v9 set to true, for geared extruder set to false
#define X_HOME_DIR 1
#define Y_HOME_DIR 1
#define Z_HOME_DIR 1
#define min_software_endstops true // If true, axis won't move to coordinates less than HOME_POS.
#define max_software_endstops true  // If true, axis won't move to coordinates greater than the defined lengths below.
#define X_MAX_POS 100
#define X_MIN_POS -100
#define Y_MAX_POS 100
#define Y_MIN_POS -100
#define Z_MAX_POS MANUAL_Z_HOME_POS
#define Z_MIN_POS 0
#define X_MAX_LENGTH (X_MAX_POS - X_MIN_POS)
#define Y_MAX_LENGTH (Y_MAX_POS - Y_MIN_POS)
#define Z_MAX_LENGTH (Z_MAX_POS - Z_MIN_POS)
#define MANUAL_HOME_POSITIONS  // If defined, MANUAL_*_HOME_POS below will be used
#define BED_CENTER_AT_0_0  // If defined, the center of the bed is at (X=0, Y=0)
#define MANUAL_X_HOME_POS 0
#define MANUAL_Y_HOME_POS 0
#define MANUAL_Z_HOME_POS Z_HOME_HEIGTH // For delta: Distance between nozzle and print surface after homing. Is set at line 130
#define NUM_AXIS 4 // The axis order in all axis related arrays is X, Y, Z, E
#define HOMING_FEEDRATE {50*60, 50*60, 50*60, 0}  // set the homing speeds (mm/min)
#define StepsPerRotation 3200.0
#define TopPulleyTeeth 16.0
#define ToothSpacing 2.0
#define XPulleyCircumference 452.0
#define YPulleyCircumference 451.0
#define ZPulleyCircumference 299.0
#define XDegrees 360.0
#define YDegrees 360.0
#define ZDegrees 231.0
#define XPulleyCircum XPulleyCircumference*360.0/XDegrees
#define YPulleyCircum YPulleyCircumference*360.0/YDegrees
#define ZPulleyCircum ZPulleyCircumference*360.0/ZDegrees
#define BeltThickness 1.49
#define ToothDepth 0.74
#define XPulleyEff ((XPulleyCircum/(2*DELTA_PI)) + (BeltThickness - ToothDepth))*2*DELTA_PI
#define YPulleyEff ((YPulleyCircum/(2*DELTA_PI)) + (BeltThickness - ToothDepth))*2*DELTA_PI
#define ZPulleyEff ((ZPulleyCircum/(2*DELTA_PI)) + (BeltThickness - ToothDepth))*2*DELTA_PI
#define XStepsPulley ToothSpacing*StepsPerRotation*TopPulleyTeeth/(XPulleyEff*1.8)
#define YStepsPulley ToothSpacing*StepsPerRotation*TopPulleyTeeth/(YPulleyEff*1.8)
#define ZStepsPulley ToothSpacing*StepsPerRotation*TopPulleyTeeth/(ZPulleyEff*1.8)
#define DEFAULT_AXIS_STEPS_PER_UNIT   {XStepsPulley, YStepsPulley, ZStepsPulley, 610.2}
#define DEFAULT_MAX_FEEDRATE          {50, 50, 50, 40}    // (mm/sec)
#define DEFAULT_MAX_ACCELERATION      {400,400,400,3000}    // X, Y, Z, E maximum start speed for accelerated moves. E default values are good for skeinforge 40+, for older versions raise them a lot.
#define DEFAULT_ACCELERATION          400    // X, Y, Z and E max acceleration in mm/s^2 for printing moves
#define DEFAULT_RETRACT_ACCELERATION  3000   // X, Y, Z and E max acceleration in mm/s^2 for retracts
#define DEFAULT_XYJERK                20.0    // (mm/sec)
#define DEFAULT_ZJERK       DEFAULT_XYJERK    // same as xY jerk for delta
#define DEFAULT_EJERK                 5.0    // (mm/sec)
#define CUSTOM_M_CODES
  #define CUSTOM_M_CODE_SET_Z_PROBE_OFFSET 851 // seems large, is default with marlin
  #define Z_PROBE_OFFSET_RANGE_MIN -15
  #define Z_PROBE_OFFSET_RANGE_MAX -5
#define PLA_PREHEAT_HOTEND_TEMP 180
#define PLA_PREHEAT_HPB_TEMP 70
#define PLA_PREHEAT_FAN_SPEED 255   // Insert Value between 0 and 255
#define ABS_PREHEAT_HOTEND_TEMP 240
#define ABS_PREHEAT_HPB_TEMP 100
#define ABS_PREHEAT_FAN_SPEED 255   // Insert Value between 0 and 255
#define SOFT_PWM_SCALE 0
#define FILAMENT_SENSOR_EXTRUDER_NUM	0  //The number of the extruder that has the filament sensor (0,1,2)
#define MEASUREMENT_DELAY_CM			14  //measurement delay in cm.  This is the distance from filament sensor to middle of barrel
#define DEFAULT_NOMINAL_FILAMENT_DIA  3.0  //Enter the diameter (in mm) of the filament generally used (3.0 mm or 1.75 mm) - this is then used in the slicer software.  Used for sensor reading validation
#define MEASURED_UPPER_LIMIT          3.30  //upper limit factor used for sensor reading validation in mm
#define MEASURED_LOWER_LIMIT          1.90  //lower limit factor for sensor reading validation in mm
#define MAX_MEASUREMENT_DELAY			20  //delay buffer size in bytes (1 byte = 1cm)- limits maximum measurement delay allowable (must be larger than MEASUREMENT_DELAY_CM  and lower number saves RAM)
#define DEFAULT_MEASURED_FILAMENT_DIA  DEFAULT_NOMINAL_FILAMENT_DIA  //set measured to nominal initially
#include "Configuration_adv.h"
#include "thermistortables.h"

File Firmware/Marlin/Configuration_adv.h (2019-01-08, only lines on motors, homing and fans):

#define CONTROLLERFAN_PIN -1 //Pin used for the fan to cool controller (-1 to disable)
#define EXTRUDER_0_AUTO_FAN_PIN   -1
#define EXTRUDER_1_AUTO_FAN_PIN   -1
#define EXTRUDER_2_AUTO_FAN_PIN   -1
#define ENDSTOPS_ONLY_FOR_HOMING // If defined the endstops will only be used for homing
  #define X_HOME_POS MANUAL_X_HOME_POS
  #define Y_HOME_POS MANUAL_Y_HOME_POS
  #define Z_HOME_POS MANUAL_Z_HOME_POS
#define X_HOME_RETRACT_MM 5
#define Y_HOME_RETRACT_MM 5
#define Z_HOME_RETRACT_MM 5 // deltas need the same for all three axis
#define MICROSTEP1 LOW,LOW
#define MICROSTEP2 HIGH,LOW
#define MICROSTEP4 LOW,HIGH
#define MICROSTEP8 HIGH,HIGH
#define MICROSTEP16 HIGH,HIGH
#define MICROSTEP_MODES {16,16,16,16,16} // [1,2,4,8,16]
#define DIGIPOT_MOTOR_CURRENT {135,135,135,135,135} // Values 0-255 (RAMBO 135 = ~0.75A, 185 = ~1A)
#define DIGIPOT_I2C_MOTOR_CURRENTS {1.0, 1.0, 1.0, 1.0, 1.0, 1.0, 1.0, 1.0}

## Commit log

2014-06-26 second commit
    [Pulley_GT2_30-tooth.stl, Pulley_GT2_30-tooth_with_clamp.stl, Pulley_GT2_30-tooth_with_clamp_4mm_centre.stl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]
2014-06-26 4th commit
    [Pulley_GT2_30-tooth.stl, Pulley_GT2_30-tooth_with_clamp.stl, Pulley_GT2_30-tooth_with_clamp_4mm_centre.stl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]
2014-06-27 added choosing pulley.txt
2014-06-27 tidied stls and directory structure
    [motor-mount-draft1.stl, motor-mount-export2.stl, motor-mount-platter1.amf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]
2014-06-27 renamed some files
    [Pulley_GT2_30-tooth.stl, Pulley_GT2_30-tooth_with_clamp.stl, Pulley_GT2_30-tooth_with_clamp_4mm_centre.stl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]
2014-06-30 added files, updated TODO
    [spacers v0.1.FCStd, spacers v0.1.stl]
2014-07-04 updated TODO, added new stls
    [Pulley_GT2_30-tooth.stl, Pulley_GT2_30-tooth_with_clamp.stl, Pulley_GT2_30-tooth_with_clamp_4mm_centre.stl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]
2014-07-08 added new files
    [brackets - all v0.5.stl, motor_mount.FCStd, motor_mount.stl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]
2014-07-14 added and improved many drawings
    [assembly.FCStd, frame.FCStd, motor_mount.FCStd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]
2014-07-17 changed directory structure
    [assembly.FCStd, brackets - all v0.5.stl, frame.FCStd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]
2014-07-30 added new files, changed directory structure
    [hexagon_constrained.FCStd, motor_mount.FCStd, motor_mount.stl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]
2014-08-02 updated upperarms, pulley beltclamp was printed and improved
    [arm_spacer_6mm_rad_12mm_tall.stl, arm_spacer_6mmrad_12mm_tall.FCStd, pulley - v0.9.FCStd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]
2014-08-09 Changed upperarms and added new files
    [arm_tube_holders.FCStd, balljoint2.2.stl, hexagon_constrained.FCStd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]
2014-08-09 changed file name
    [arm_spacer_6mmrad_12mm_tall.stl]
2014-08-13 More iterations, more improvements
    [pulley_v0.9.6.FCStd, pulley_v0.9.6.stl, upperarm v2.2.5.FCStd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]
2014-11-30 added endstop files, added experimental patch for marlin for nonlinear delta printers
    [arm_spacer_fat.FCStd, arm_spacer_fat.stl, arm_spacer_skinny.stl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]
2014-12-09 improved commenting in marlin patch and reworked steps per mm code
2014-12-11 fixed belt clamp placement on pulley_fat_v0.9.4
    [pulley_fat_v0.9.4.FCStd, pulley_fat_v0.9.4.stl]
2014-12-11 added newer improved pulley
    [pulley_halfmoon_v0.9.4.FCStd, pulley_halfmoon_v0.9.4.stl]
2014-12-11 renamed files to more descriptive names
    [effector.stl, effector_diagonal_rod_tube.FCStd, effector_diagonal_rod_tubes.stl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]
2014-12-11 removed empty/outdated directories
    [arm_spacer_fat.FCStd, arm_spacer_fat.stl, arm_spacer_skinny.stl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]
2014-12-11 renamed pulley_mounts
    [pulley_mounts.stl]
2014-12-11 deleted old folder
    [brackets - all v0.5.stl, mount bottom positioned flat v0.5.stl, mount bottom positioned upright v0.5.stl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]
2014-12-11 renamed to indicate design is outdated
    [assembly (outdated).FCStd, frame_mockup (outdated).FCStd]
2014-12-12 added more items to bill of materials
2014-12-12 tweaked nut trap position
    [pulley_mount.stl, pulley_mounts.stl]
2014-12-12 discontinuing the thinner pulley version
    [pulley_skinny_v0.9.6.FCStd, pulley_skinny_v0.9.6.stl, pulley_v0.9.4.FCStd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]
2014-12-16 slightly enlarged belt slit so that it is not so tight
    [pulley_halfmoon_v0.9.4.FCStd, pulley_halfmoon_v0.9.4.stl]
2014-12-16 recomend half pulleys over the full round ones
2014-12-16 changed pulley naming from halfmoon pulleys to half pulleys
    [pulley_half_v0.9.4.FCStd, pulley_half_v0.9.4.stl]
2015-01-05 resized upper arm length, removing extra long and short holes for traxxas rod joints
    [upperarm.FCStd, upperarm.stl]
2015-01-06 renamed upperarm files
    [upperarm_160mm.FCStd, upperarm_160mm.stl, upperarm_old_180_160_130mm lengths.FCStd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]
2015-01-09 added jhead end effector clamp with mount for 50mm fan
    [effctor_clamp+fan_mount.stl, effector_jhead_clamp+fan_mount.FCStd, jhead_clamp.FCStd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]
2015-01-09 renamed file
    [effector_jhead_clamp.FCStd, jhead_clamp.stl]
2015-01-12 improved upperarm_spacer and where it connects to the upperarm
    [upperarm_160mm.FCStd, upperarm_160mm.stl, upperarm_spacer.FCStd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]
2015-01-13 rotated arm stl to fit diagonally on platter
    [upperarm_160mm.stl]
2015-01-26 emphasize that this printer is experimental in the readme
2019-01-08 Added firmware
    [Configuration.h, Configuration_adv.h, Menu Plans.xlsx]
